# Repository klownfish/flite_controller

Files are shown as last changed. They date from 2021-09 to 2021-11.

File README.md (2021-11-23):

# Flite Controller
## the world smallest (maybe) all in one flight controller

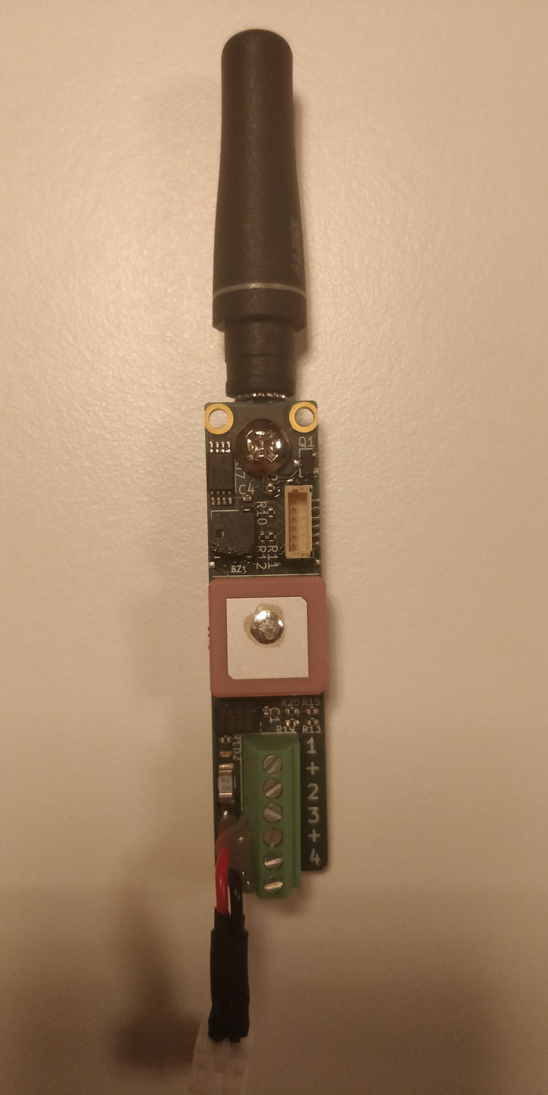
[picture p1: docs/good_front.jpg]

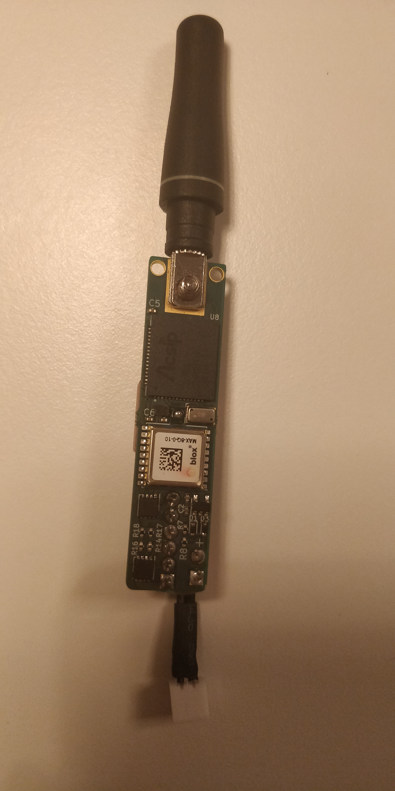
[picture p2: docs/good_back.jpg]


### Features
1. Accelerometer
1. Barometer
1. 4x pyro channels
1. GPS
1. Long range telemetry
1. Built-in antennas
1. low power processor
1. high frequency onboard storage of data
1. best of all, it fits in a 17mm body tube

### technical details
The whole board is built around the AcSIP S76S. It is a "System On A Chip" containing a LoRa modem and a STM32L073xZ.

The telemetry antenna is connected to the board using friction and a screw while the GPS uses an onboard patch antenna. Due to the small size the RF-section is very poorly designed but the GPS line has an amplifier and a filter at the very least. The telemetry range is probably around 15km but at the very least 10km.

It has an expansion port with 3V3, UART, BOOT0 and and IO pin for programming and connecting accessories. Two SWD pads are also exposed but unused at the moment.

The 200g accelerometer used is the ADXL343 but in hindsight I should have put a bmi088 or bmx160 since no rocket will ever reach 200g (I was fucked by the chip shortage as well). MS5607-02BA is the pressure sensor but they are pretty much all the same. The current GPS module is the ublox m8 but anything with MAX form-factor will work.

It's a 4 layer PCB with a SIG/SIG/GND/SIG stackup. Designed for production with Aisler but they are usually slow and expensive. European though so they don't have suicide nets or shit out a bunch of toxins which is a plus!

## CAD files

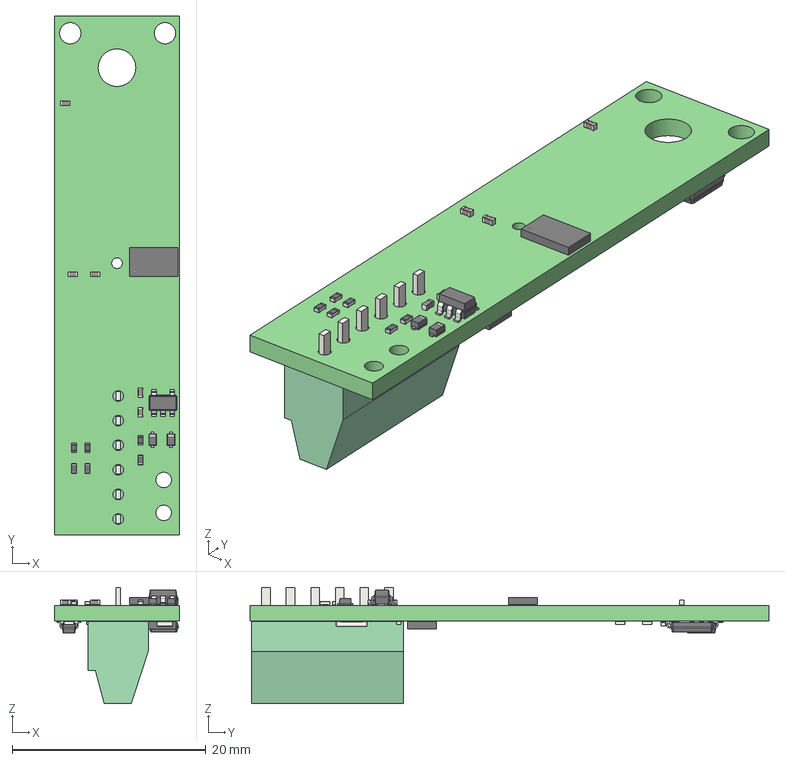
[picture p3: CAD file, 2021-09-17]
schematic/mini_controller.step
13.0 x 53.6 x 12.0 mm

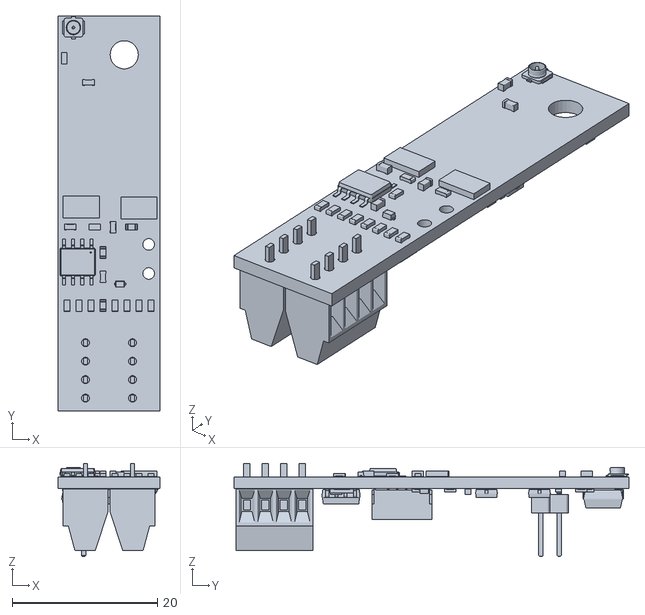
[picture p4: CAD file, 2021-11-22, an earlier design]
old/mini_controller2/mini_controller.stl
14.0 x 54.4 x 12.8

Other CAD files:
schematic/mini_controller.stl

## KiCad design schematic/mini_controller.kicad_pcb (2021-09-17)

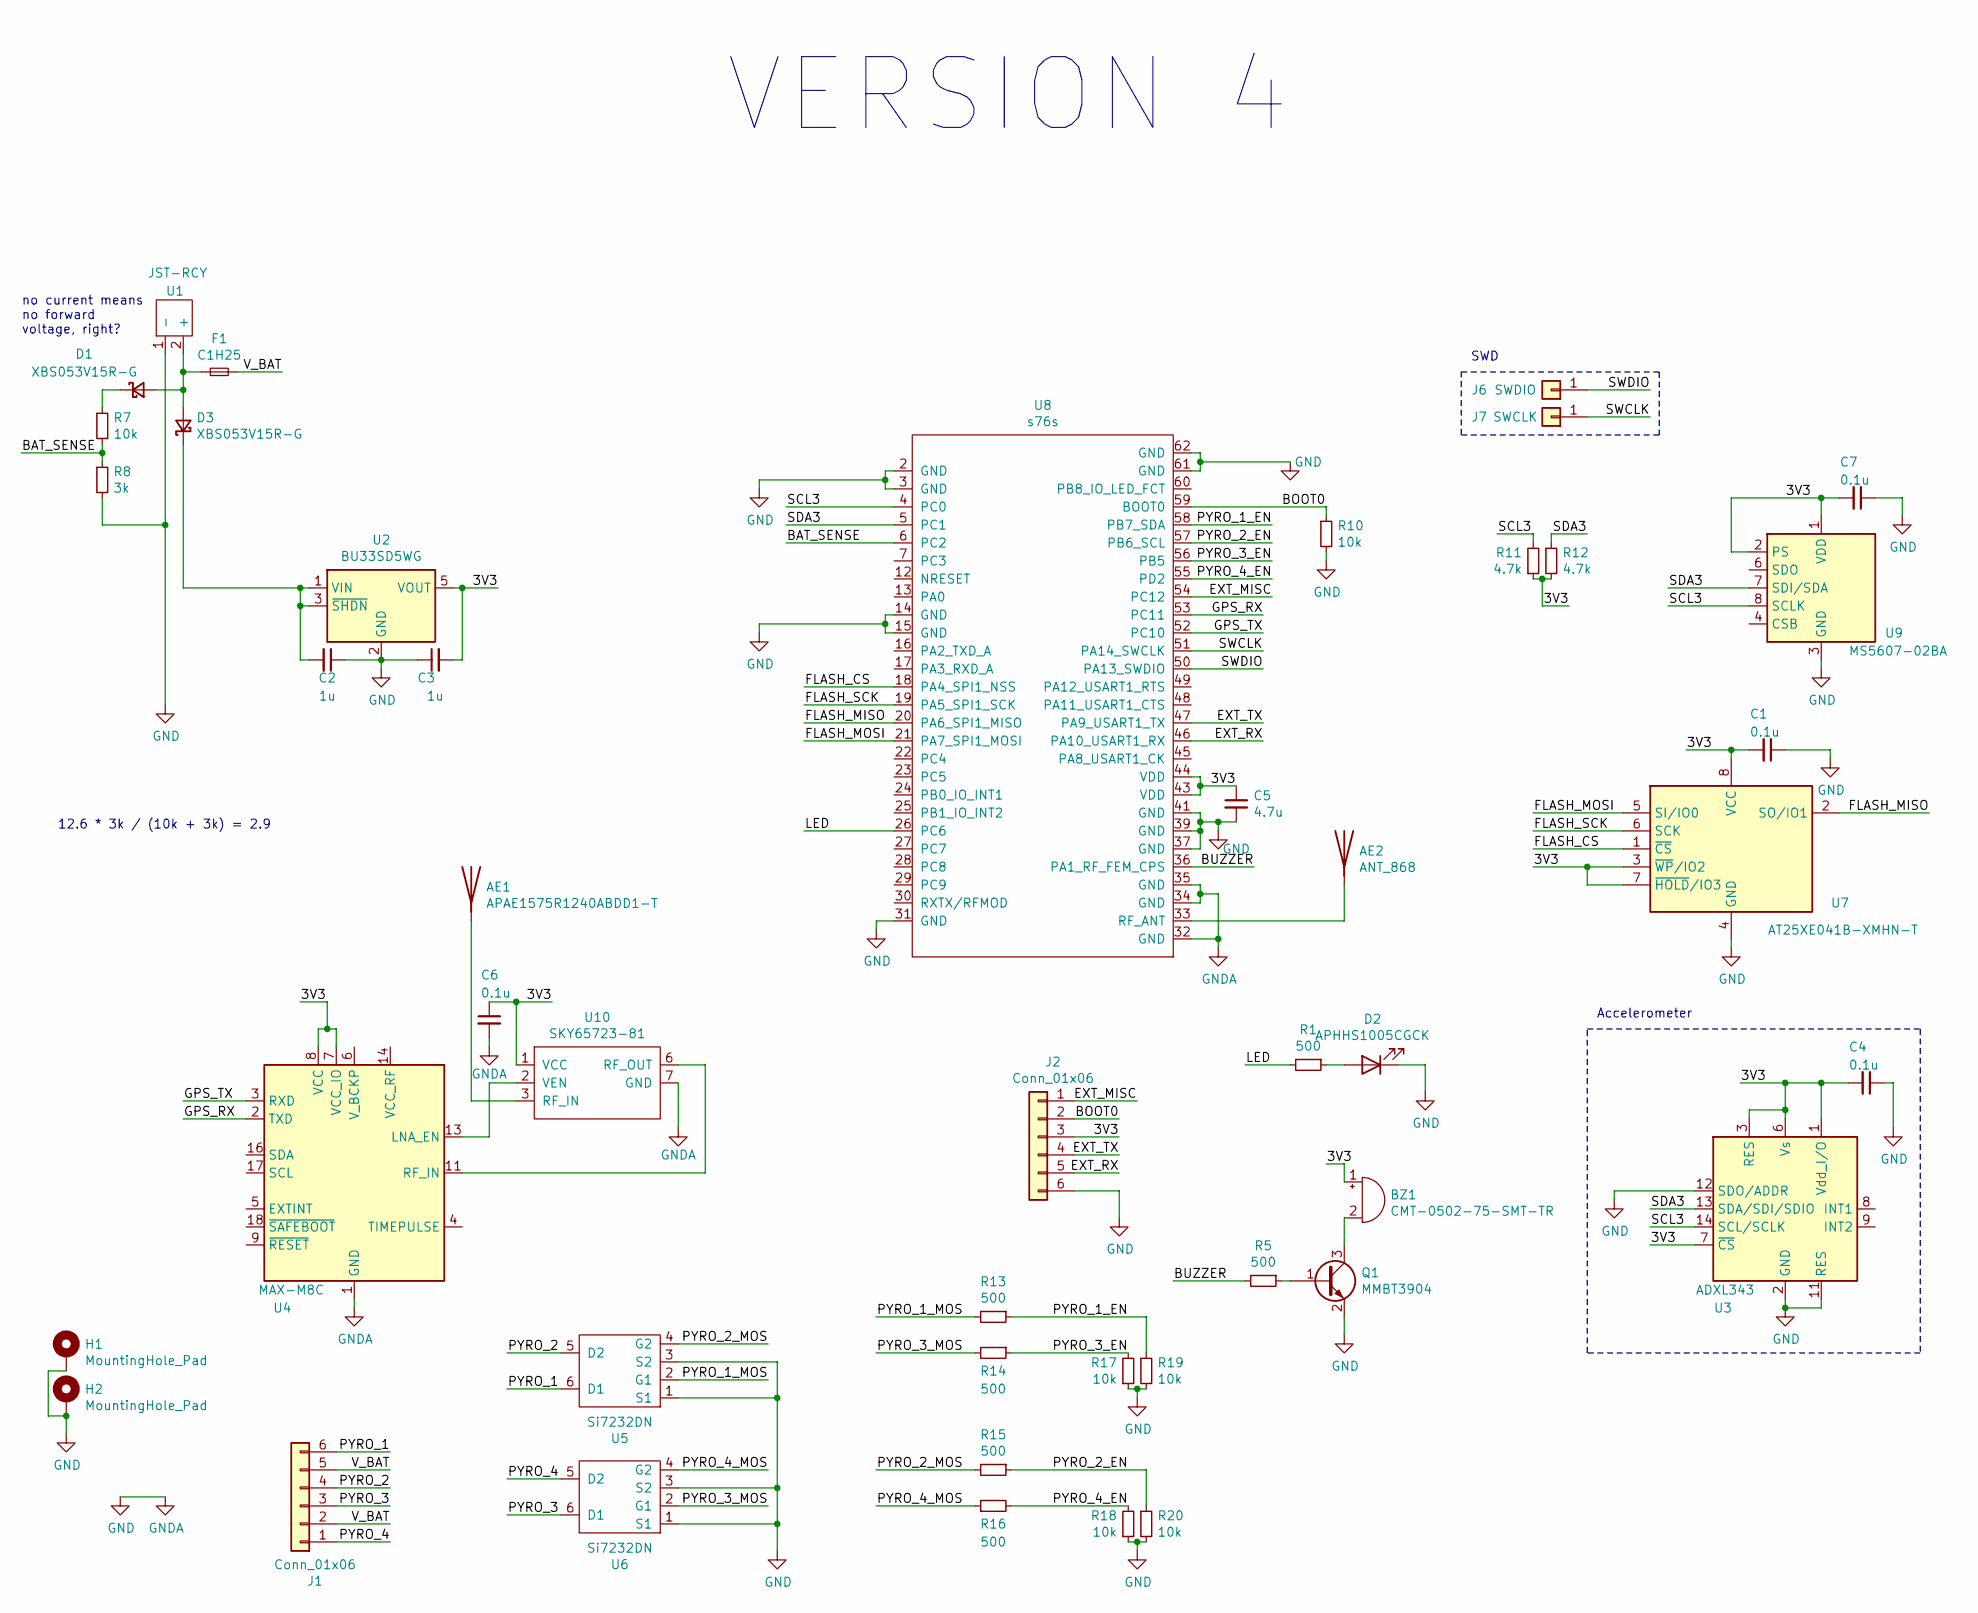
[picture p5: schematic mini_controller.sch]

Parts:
AE1: APAE1575R1240ABDD1-T
AE2: ANT_868; ANT-868-PW-LP
BZ1: CMT-0502-75-SMT-TR; XDCR_CMT-0502-75-SMT-TR
C1, C4, C6, C7: 0.1u; C_0402_1005Metric
C2, C3: 1u; C_0402_1005Metric
C5: 4.7u; C_0402_1005Metric
D1, D3: XBS053V15R-G; D_SOD-523
D2: APHHS1005CGCK; D_0402_1005Metric
F1: C1H25; Fuse_1206_3216Metric_Pad1.42x1.75mm_HandSolder
H1, H2: MountingHole_Pad; MountingHole_2.2mm_M2_ISO7380_Pad_TopOnly
J1: Conn_01x06; TerminalBlock_Phoenix_MPT-0,5-6-2.54_1x06_P2.54mm_Horizontal
J2: Conn_01x06; JST_SH_BM06B-SRSS-TB_1x06-1MP_P1.00mm_Vertical
J6: SWDIO; just_a_pad
J7: SWCLK; just_a_pad
Q1: MMBT3904; SOT-23
R1, R5, R13, R14, R15, R16: 500; R_0402_1005Metric
R7, R10, R17, R18, R19, R20: 10k; R_0402_1005Metric
R8: 3k; R_0402_1005Metric
R11, R12: 4.7k; R_0402_1005Metric
U1: JST-RCY; xt30_pigtail
U2: BU33SD5WG; SOT-23-5
U3: ADXL343; LGA-14_3x5mm_P0.8mm_LayoutBorder1x6y
U4: MAX-M8C; ublox_MAX
U5, U6: Si7232DN; Vishay_PowerPAK_1212-8_Dual
U7: AT25XE041B-XMHN-T; TSSOP-8_4.4x3mm_P0.65mm
U8: s76s
U9: MS5607-02BA; LGA-8_3x5mm_P1.25mm
U10: SKY65723-81; Skyworks_SKY65404-31

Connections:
/3V3: BZ1.1 (-), C1.2, C3.2, C4.2, C5.1, C6.1, C7.2, J2.3, R11.1, R12.2, U2.5 (VOUT), U3.1 (Vdd_I/O), U3.3 (RES), U3.6 (Vs), U3.7 (~CS), U4.7 (VCC_IO), U4.8 (VCC), U7.3 (~WP~/IO2), U7.7 (~HOLD~/IO3), U7.8 (VCC), U8.43 (VDD), U8.44 (VDD), U9.1 (VDD), U9.2 (PS), U10.1 (VCC)
/BAT_SENSE: R7.2, R8.1, U8.6 (PC2)
/BOOT0: J2.2, R10.1, U8.59 (BOOT0)
/BUZZER: R5.2, U8.36 (PA1_RF_FEM_CPS)
/EXT_MISC: J2.1, U8.54 (PC12)
/EXT_RX: J2.5, U8.46 (PA10_USART1_RX)
/EXT_TX: J2.4, U8.47 (PA9_USART1_TX)
/FLASH_CS: U7.1 (~CS), U8.18 (PA4_SPI1_NSS)
/FLASH_MISO: U7.2 (SO/IO1), U8.20 (PA6_SPI1_MISO)
/FLASH_MOSI: U7.5 (SI/IO0), U8.21 (PA7_SPI1_MOSI)
/FLASH_SCK: U7.6 (SCK), U8.19 (PA5_SPI1_SCK)
/GPS_RX: U4.2 (TXD), U8.53 (PC11)
/GPS_TX: U4.3 (RXD), U8.52 (PC10)
/LED: R1.2, U8.26 (PC6)
/PYRO_1: J1.6, U5.6 (D1)
/PYRO_1_EN: R13.1, R19.1, U8.58 (PB7_SDA)
/PYRO_1_MOS: R13.2, U5.2 (G1)
/PYRO_2: J1.4, U5.5 (D2)
/PYRO_2_EN: R15.1, R20.1, U8.57 (PB6_SCL)
/PYRO_2_MOS: R15.2, U5.4 (G2)
/PYRO_3: J1.3, U6.6 (D1)
/PYRO_3_EN: R14.1, R17.2, U8.56 (PB5)
/PYRO_3_MOS: R14.2, U6.2 (G1)
/PYRO_4: J1.1, U6.5 (D2)
/PYRO_4_EN: R16.2, R18.2, U8.55 (PD2)
/PYRO_4_MOS: R16.1, U6.4 (G2)
/SCL3: R11.2, U3.14 (SCL/SCLK), U8.4 (PC0), U9.8 (SCLK)
/SDA3: R12.1, U3.13 (SDA/SDI/SDIO), U8.5 (PC1), U9.7 (SDI/SDA)
/SWCLK: J7.1, U8.51 (PA14_SWCLK)
/SWDIO: J6.1, U8.50 (PA13_SWDIO)
/V_BAT: F1.2, J1.2, J1.5
GND: C1.1, C2.1, C3.1, C4.1, C5.2, C6.2, C7.1, D2.1 (K), H1.1, H2.1, J2.6, Q1.2 (E), R8.2, R10.2, R17.1, R18.1, R19.2, R20.2, U1.1 (-), U2.2 (GND), U3.2 (GND), U3.4 (GND), U3.5 (GND), U3.11 (RES), U3.12 (SDO/ADDR), U4.1 (GND), U4.10 (GND), U4.12 (GND), U5.1 (S1), U5.3 (S2), U6.1 (S1), U6.3 (S2), U7.4 (GND), U8.2 (GND), U8.3 (GND), U8.14 (GND), U8.15 (GND), U8.31 (GND), U8.32 (GND), U8.34 (GND), U8.35 (GND), U8.37 (GND), U8.39 (GND), U8.41 (GND), U8.61 (GND), U8.62 (GND), U9.3 (GND), U10.7 (GND)
unnamed: AE1.1, U10.3 (RF_IN)
unnamed: AE2.1, U8.33 (RF_ANT)
unnamed: BZ1.2 (+), Q1.3 (C)
unnamed: C2.2, D3.1 (K), U2.1 (VIN), U2.3 (~SHDN)
unnamed: D1.1 (K), R7.1
unnamed: D1.2 (A), D3.2 (A), F1.1, U1.2 (+)
unnamed: D2.2 (A), R1.1
unnamed: Q1.1 (B), R5.1
unnamed: U9.4 (CSB), U9.5 (CSB)
unnamed: U4.13 (LNA_EN), U10.2 (VEN)
unnamed: U4.11 (RF_IN), U10.6 (RF_OUT)

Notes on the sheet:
12.6 * 3k / (10k + 3k) = 2.9
no current means no forward voltage, right?
VERSION 4
SWD
Accelerometer

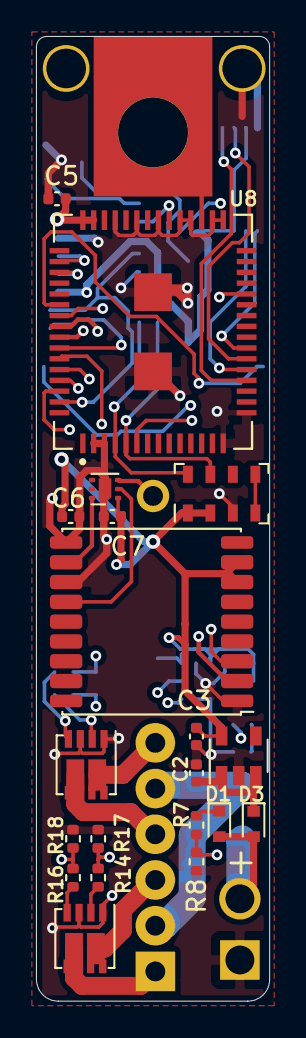
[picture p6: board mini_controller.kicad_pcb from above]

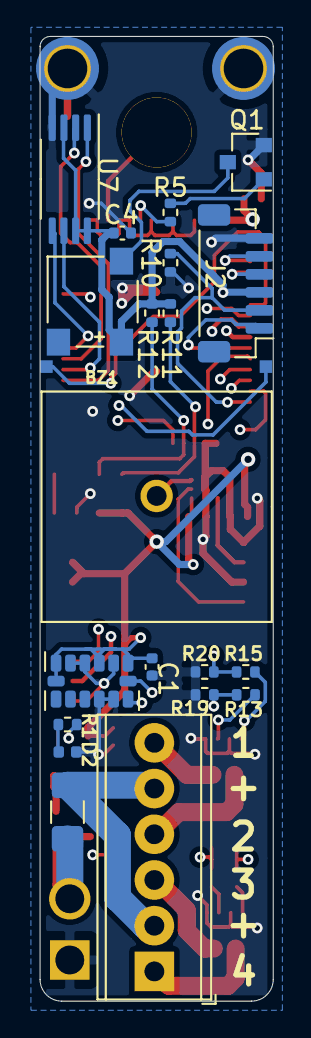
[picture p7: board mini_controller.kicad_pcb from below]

Board: 4 copper layers, 13.0 x 53.6 mm, 46 parts (24 on the bottom side), 43 nets.

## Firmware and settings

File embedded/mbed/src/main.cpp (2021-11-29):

#include "mbed.h"

DigitalIn pyro_1(PB_7);
DigitalIn pyro_2(PB_6);
DigitalIn pyro_3(PB_5);
DigitalIn pyro_4(PD_2);
DigitalIn ext_misc(PC_12);
BufferedSerial gps_serial(PC_10, PC_11, 9600);
BufferedSerial ext_serial(PA_9, PA_10, 115200);
PwmOut buzzer(PA_1);
//PwmOut led(PC_6);
DigitalOut led(PC_6);
SPI flash_spi(PA_7, PA_6, PA_5, PA_4);
//SPI lora_spi(PB_15, PB_14, PB_13, PB_12); this could be wrong
AnalogIn bat_read(PC_0);
I2C i2c(PC_1, PC_0);

int main(void) {
    led.write(1);
    while(1){
        led.write(1);
        wait_us(1000000);
        led.write(0);
        wait_us(1000000);
    }
}

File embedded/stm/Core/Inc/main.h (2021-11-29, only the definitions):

#define BUZZER_Pin GPIO_PIN_1
#define BUZZER_GPIO_Port GPIOA
#define FLASH_CS_Pin GPIO_PIN_4
#define FLASH_CS_GPIO_Port GPIOA
#define LED_Pin GPIO_PIN_6
#define LED_GPIO_Port GPIOC
#define EXT_TX_Pin GPIO_PIN_9
#define EXT_TX_GPIO_Port GPIOA
#define EXT_RX_Pin GPIO_PIN_10
#define EXT_RX_GPIO_Port GPIOA
#define EXT_MISC_Pin GPIO_PIN_12
#define EXT_MISC_GPIO_Port GPIOC
#define PYRO_4_Pin GPIO_PIN_2
#define PYRO_4_GPIO_Port GPIOD
#define PYRO_3_Pin GPIO_PIN_5
#define PYRO_3_GPIO_Port GPIOB
#define PYRO_2_Pin GPIO_PIN_6
#define PYRO_2_GPIO_Port GPIOB
#define PYRO_1_Pin GPIO_PIN_7
#define PYRO_1_GPIO_Port GPIOB

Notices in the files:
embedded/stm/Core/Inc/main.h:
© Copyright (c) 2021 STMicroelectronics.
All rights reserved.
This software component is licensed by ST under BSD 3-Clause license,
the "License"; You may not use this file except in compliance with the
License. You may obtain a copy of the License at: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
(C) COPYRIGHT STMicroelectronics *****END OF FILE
